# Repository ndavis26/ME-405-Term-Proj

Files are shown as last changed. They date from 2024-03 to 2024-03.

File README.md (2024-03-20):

README.md
=========
Author: Nathaniel Davis
<br>GitHub Repository Link: [ME 405 Term Project](https://github.com/ndavis26/ME-405-Term-Proj)

# Introduction

The purpose of this device is to autonomously aim a NERF blaster at a target and fire it after the program is started. The device was designed to follow a NERF turret [dueling procedure](#dueling-procedure) between two opposing teams.

It is intended for use by children, with a similar use case as other foam-flinging toys, where the goal is to pelt friends and "foes" alike with harmless foam darts. However, the use of the design can reach far beyond foam darts. Given that the sensor detects heat signatures and operates based off of the greatest heat signature, the code can be used for other applications, such as autonomous fire control, where the device would aim water at a fire's greatest heat location to douse the fire (most often its base, which is where a fire should be targeted with water).

<br/><br/>

# Hardware

## Physical Contruction

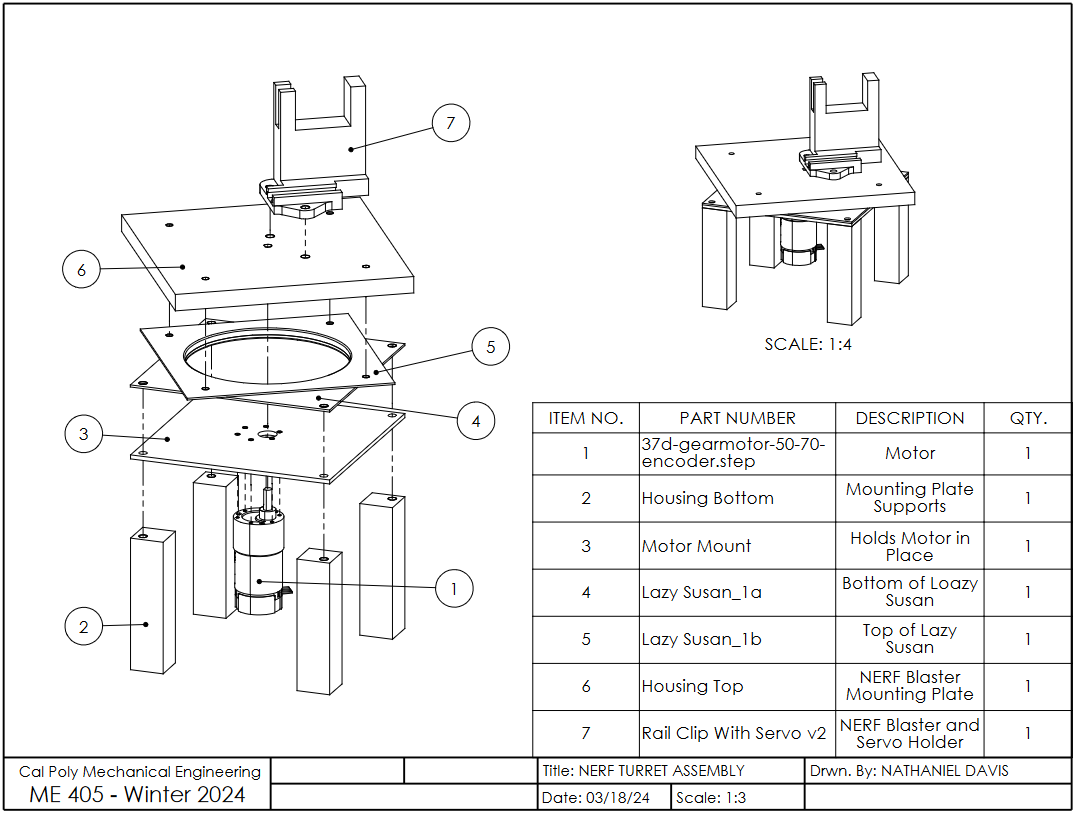
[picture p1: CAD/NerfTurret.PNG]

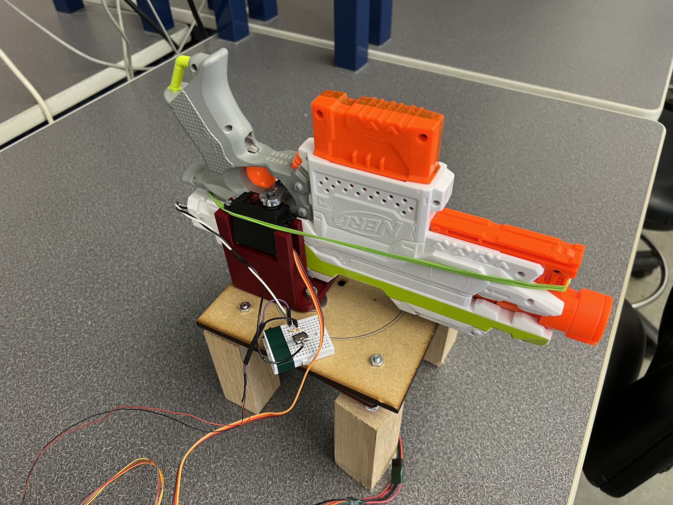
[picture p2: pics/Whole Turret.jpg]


The hardware involved features a modified NERF blaster toy to fire the darts.[^1] This blaster is staged upon a flat plate that is on top of a lazy susan bearing. On the underside of the lazy susan bearing, there is a motor mounting plate. When the motor is mounted to this plate, it connects directly to the blaster base. Although the CAD model shows a single, uniform plate for mounting the NARF blaster, the mounting plate on the current turret uses two plates stacked - one made of acrylic and another made of wood. The acrylic plate is to ensure that there is no deformation, since the motor directly drives the plate on its shaft and acrylic is extremely brittle. The wood plate ensures that there is enough thickness that the motor shaft does not stick out. A list of materials sourced from outside of the mechatronics lab is included in the [Materials](#materials) appendix.

[^1]: Given that NERF brand toys are not *guns* (which fire *bullets*), they will be referred to as *"blasters"* throughout this document (which fire *darts*).

## Circuitry

The circuitry for this device is relatively simple. There are 4 main peripheral electronics to the Nucleo. They are the main motor with encoder, the servo motor, the IR camera, and the NERF flywheels. Although all three are controlled by the Nucleo, the main motor and servo motor are powered by the 12V bench power supply and the flywheels are powered by the 6V battery pack inside of the NERF blaster. The pin connections and any relevant circuit diagrams are included below.

### Main Motor

| **Motor and Encoder Pin** | **Nucleo Pin** |
|---|---|
| Motor Power A | PB4 |
| Motor Power B | PB5 |
| Encoder V_cc | Power Supply 12V |
| Encoder Ground | GND |
| Encoder A Output | PC6 |
| Encoder B Output | PC7 |

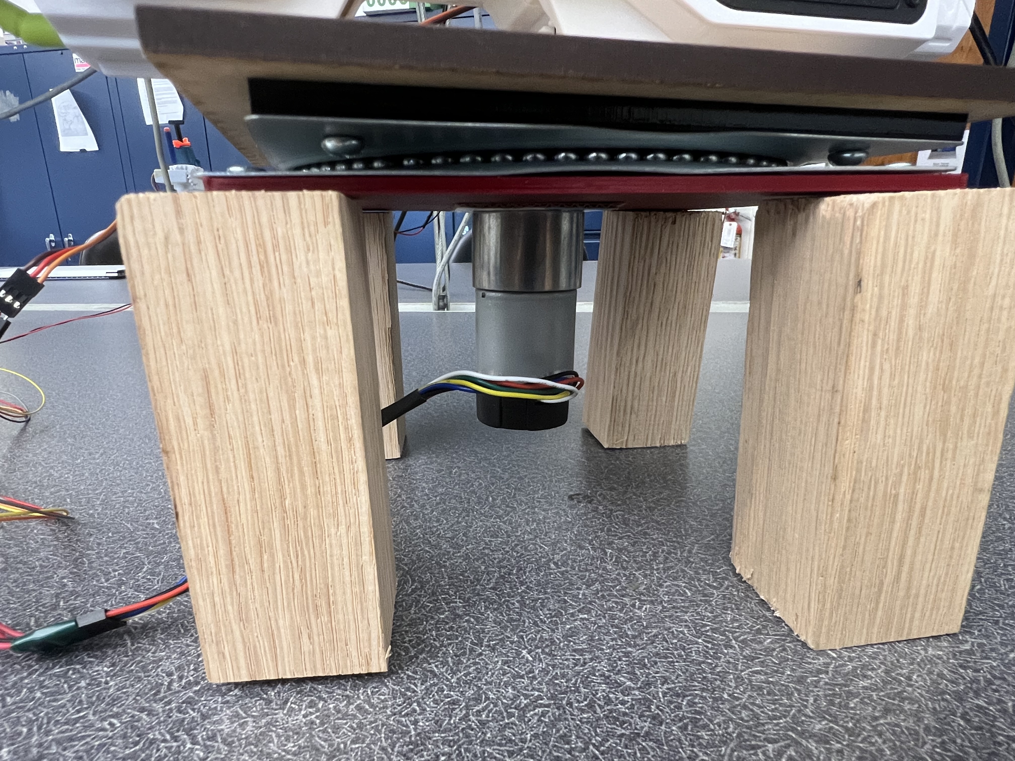
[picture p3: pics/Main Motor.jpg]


This motor has 64 ticks per revolution internally. Given that the output ratio is 50:1, the motor effectively has 3200 ticks per revolution, which is the autoreload value used in the coding.

### Servo Motor

| **Servo Motor Pin** | **Nucleo Pin** |
|---|---|
| Servo Control | PB6 |
| V_in | Power Supply 12V |
| Servo Ground | GND |

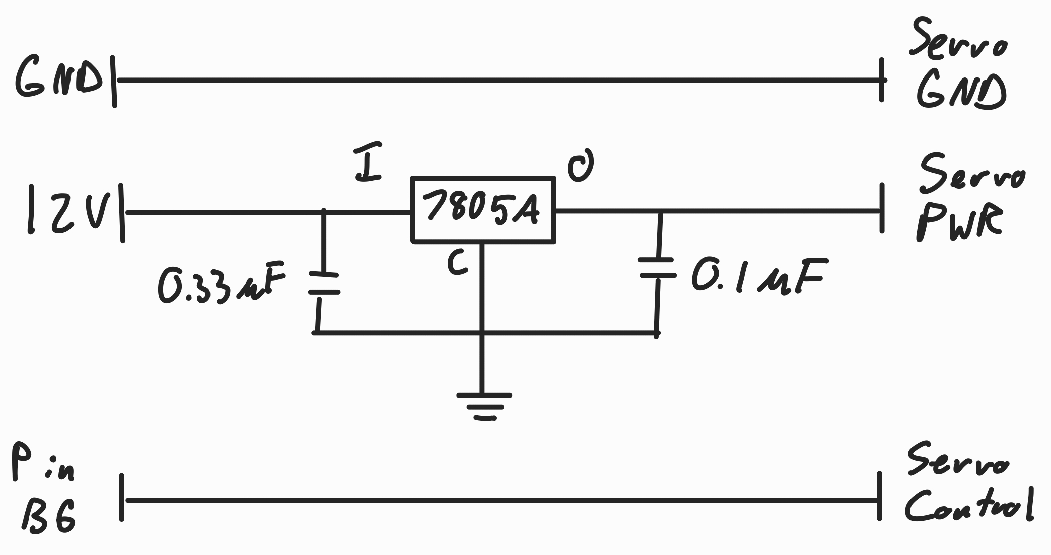
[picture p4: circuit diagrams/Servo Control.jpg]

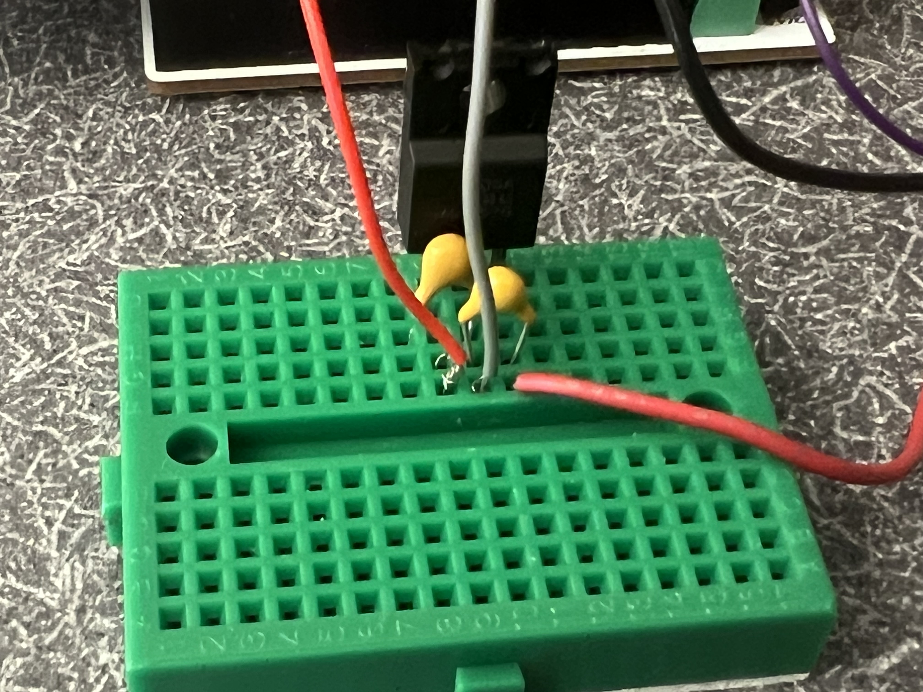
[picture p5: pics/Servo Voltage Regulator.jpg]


Since the servo motor cannot handle 12 volts of power, it must use a voltage regulator to keep the servo power at 5 volts.

### IR Camera

| **IR Camera Pin** | **Nucleo Pin** |
|---|---|
| V_in | 3V3 |
| Ground | GND |
| SDA | PB9 |
| SCL | PB8 |

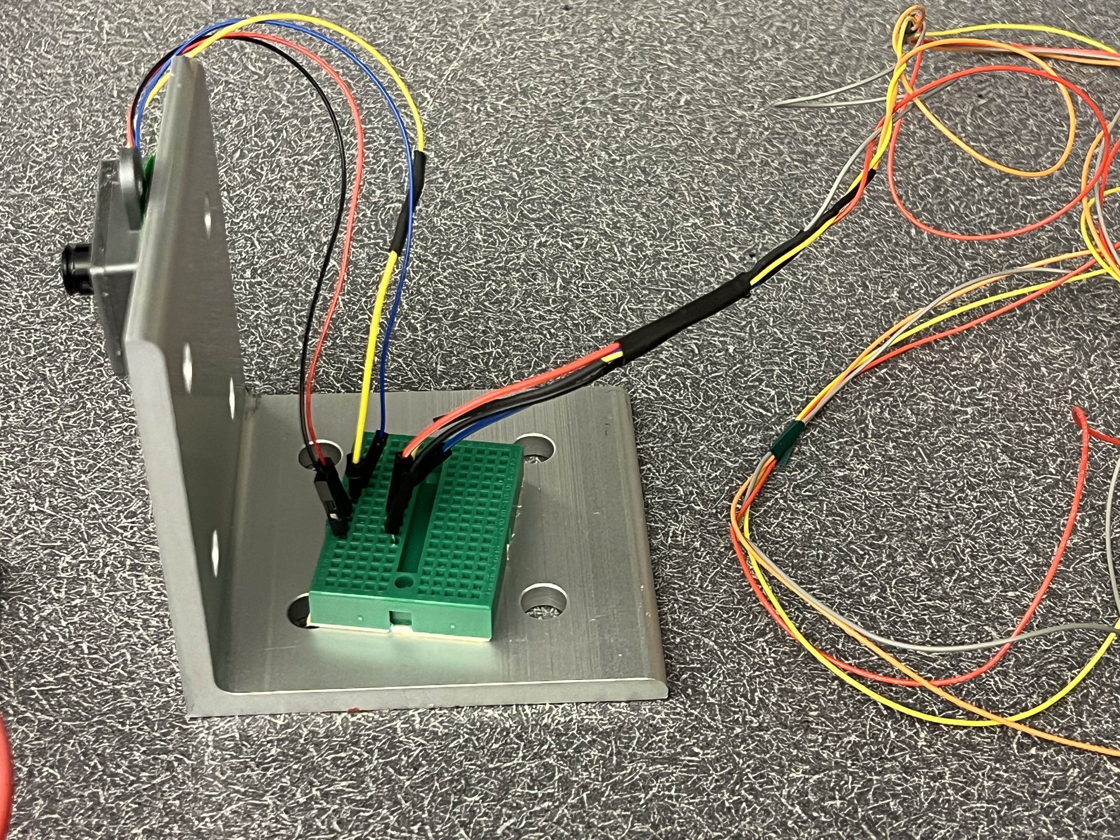
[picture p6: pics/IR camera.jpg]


### Flywheels

| **Flywheel Pin** | **Nucleo Pin** |
|---|---|
| MOSFET Gate | PC3 |
| Ground | GND |

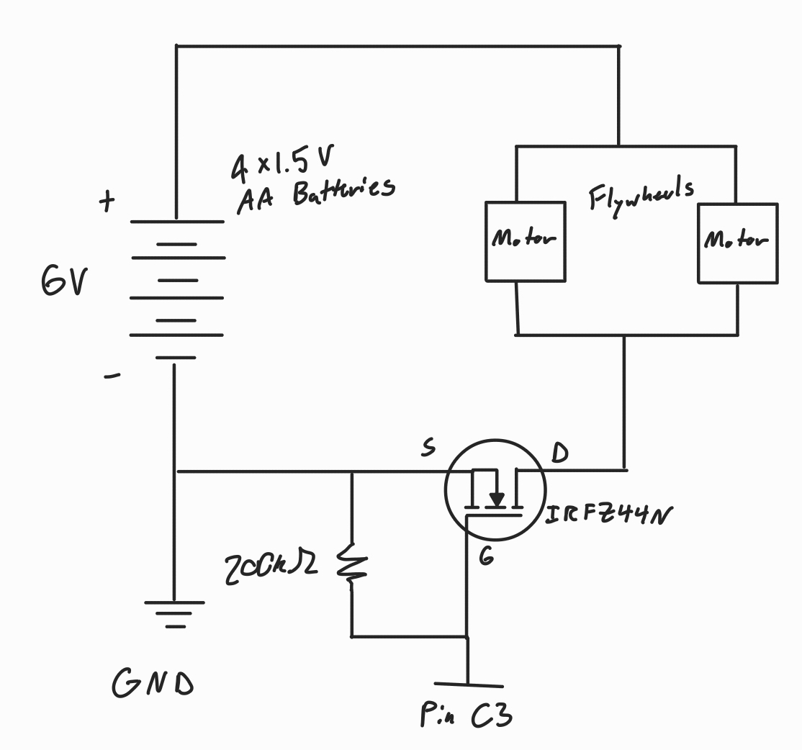
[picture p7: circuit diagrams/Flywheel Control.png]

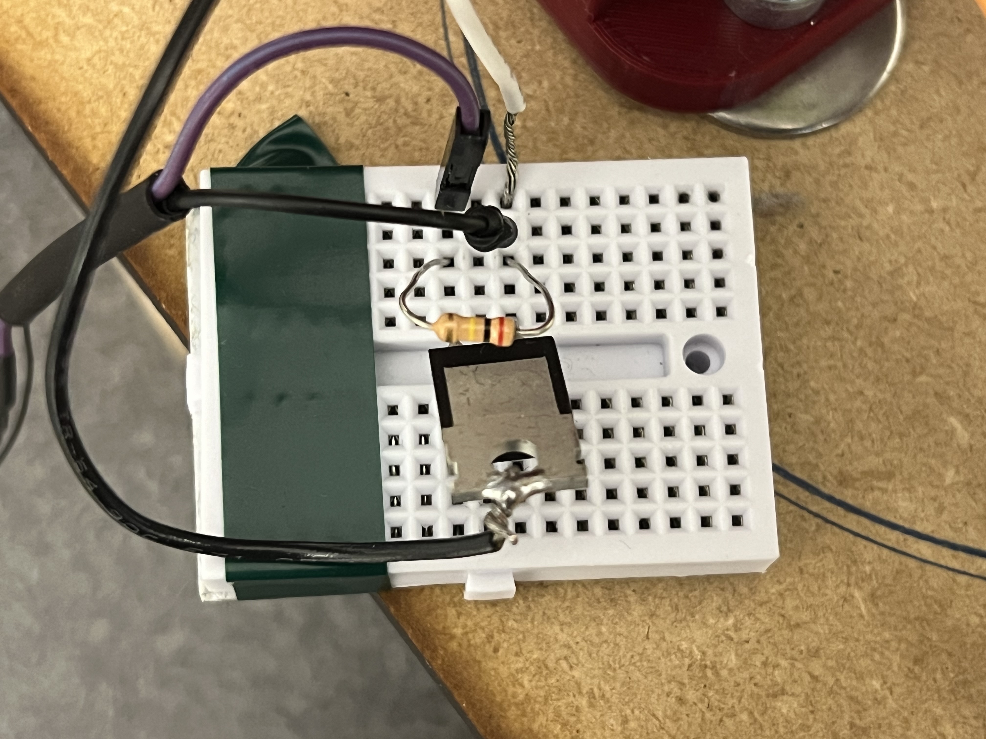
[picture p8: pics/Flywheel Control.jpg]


Pin C3 is used to control the NERF flyhweels.

<br/><br/>

# Software

The dueling is completed in 7 repeating steps, besides intialization. The peripheral(s) used during the step are shown in italics:

1. Wait for button press.
2. Turn to face opponent. *-Motor*
3. Wait 5 seconds.
4. Check current position of opponent. *-IR camera*
5. Adjust aim. *-Motor*
6. Fire. *-Servo, Flywheels*
7. Turn back around and reset to Step 1. *-Motor*

## Files

The files used are:
* [main_v3.py](https://github.com/ndavis26/ME-405-Term-Proj/blob/main/src/main_v3.py) - Holds the tasks and states of the device.
* [motor_driver_updated.py](https://github.com/ndavis26/ME-405-Term-Proj/blob/main/src/motor_driver_updated.py) - Reference for motor class object. This class sets the PWM of the motor.
* [encoder_reader_updated.py](https://github.com/ndavis26/ME-405-Term-Proj/blob/main/src/encoder_reader_updated.py) - Reference for encoder class object. This class reads the motor encoder.
* [motorwithencoder_updated.py](https://github.com/ndavis26/ME-405-Term-Proj/blob/main/src/motorwithencoder_updated.py) -  Reference for the motor controller class object. This class controls the motor through PI control.
* [servo.py](https://github.com/ndavis26/ME-405-Term-Proj/blob/main/src/servo.py) -  Reference for the servo class object. This class controls the servo through pulse width signals.
* [mlx_cam.py](https://github.com/ndavis26/ME-405-Term-Proj/blob/main/src/mlx_cam.py) - Reference for the IR camera class object. This class takes pictures using the IR camera by TWI communication. Original file is sourced from the [ME405-Support GitHub repository](https://github.com/spluttflob/ME405-Support).

The full Doxygen documentation of all the files can be found [here](https://ndavis26.github.io/ME-405-Term-Proj/).

## Tasks / States

Due to the sequential nature of the dueling procedure, only two tasks are needed. 

### Task 1: Mastermind
The first task handles the looping dueling procedure. It involves 7 states. There is only 1 intertask variable, *motor_setpoint*, which stores the motor setpoint. This task has a priority of 1 and a period of 20 ms.

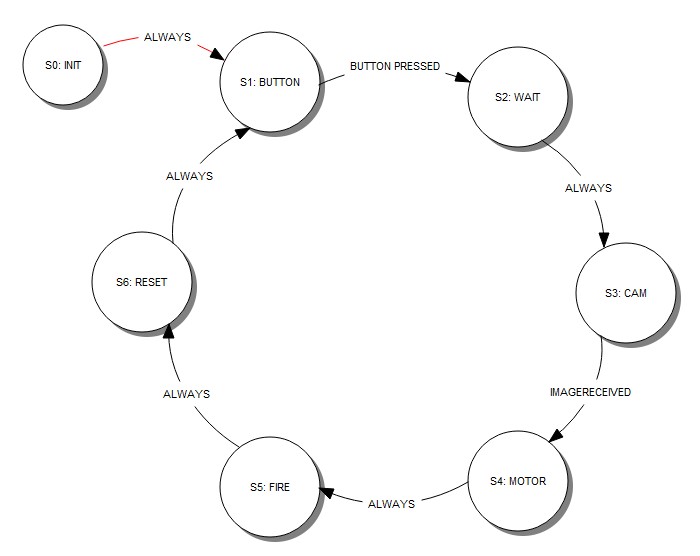
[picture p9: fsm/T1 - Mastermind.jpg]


**S0: INIT** <br>
This state intializes the system. It sets the servo control pins, the flywheel pins, the start button on the Nucleo, and initializes the IR camera.

**S1: BUTTON** <br>
Repeatedly checks if the blue button on the Nucleo has been pressed. If it has been pressed, the state transitions to state 2. If not pressed, the state does nothing and yields.

**S2: WAIT** <br>
Turns around the NERF blaster 180 degrees and waits for 5 seconds. The state accomplishes this by waiting for 10 ms intervals at a time and yielding in between each interval.

**S3: CAM** <br>
This state checks if an image has been captured from the IR camera. If no image has been captured, the state does nothing and yields. If there is an image, the state finds the line within the data with the greatest heat value sum and produces an angle to turn to.

**S4: MOTOR** <br>
Using the angle produced in state 3, the motor setpoint is adjusted to achieve the desired angle.

**S5: FIRE** <br>
This state starts the uninterruptible firing sequence:
1. Flywheels on
2. Servo pulls trigger
3. Flywheels off
4. Servo returns to its original position

**S6: RESET** <br>
Turns the blaster back around and resets to state 1.

### Task 2: Motor Control
The second task simply handles the motor control. It constantly tries to reach the motor setpoint defined by the *motor_setpoint* intertask variable. The motor controller uses PI control to accurately (albeit slowly) obtain the proper angle. There are only 2 states. This task has a priority of 1 and a period of 10 ms.

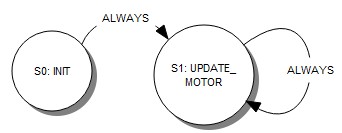
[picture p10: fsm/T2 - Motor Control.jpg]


**S0: INIT** <br>
This state intializes the motor control. Here, the motor and encoder pins are defined and the motor, encoder, and motor controller class objects are created.

**S1: UPDATE_MOTOR** <br>
Repeatedly udpates the PWM to the motor through PI control. The setpoint used is pulled from motor_setpoint.

<br/><br/>

# Results

## Testing

The overall system was tested through repeated dueling, but individual components were tested through different means. 

The motor control was tested by repeatedly having the system rotate 180 degrees as well as having it do small aiming adjustments. The Kp and Ki were then adjusted until both procedures could be performed in an acceptable amount of time. 

The camera was tested by standing at different angles relative to the IR camera and adjusting the angle it gives based on the IR picture it takes.

The flywheel and servo control were tested using the [firing test.py](https://github.com/ndavis26/ME-405-Term-Proj/blob/main/src/test/firing%20test.py) file. This test was used to tune the duration of the servo movement.

## Improvements and Recomendations

Unfortunately there are many flaws to this system.

The device can properly turn to face the opponent, check the camera, adjust accordingly, and turn on the flywheels, but is unfortunately unable to fire darts in its current state due to the servo's malfunction.

The first flaw is the trigger system. The first servo we used drew too much current, which I did not discover until later in the project. While testing the servo and firing procedure, I had been using my desktop computer as the USB power source for the Nucleo, which had sufficient current supply. However, when I began to use my laptop, the current draw (which exceeded the ~0.5 amp fuse in the USB port), it shut my laptop off. We began to search for other solutions, including using a voltage regulator combined with the 12V power supply, which only works some of the time[^2]. If the torque of the motor ever accidentally exceeds a certain amount, the voltage regulator will drop to 1 volt supplied to the servo. If given more time, a more robust servo trigger system would be devloped. It would require a combination of circuit redesign to get the current needed to the servo as well as manufacturing redesign to make sure the servo motor does not have to exert as much effort (and can pull the trigger more reliably).

[^2]: The 12V power supply also had to be set to 1.5 A to make it less likely that the current draw did not exceed the power supply's current source.

The second flaw is in the PI motor control. The first and last moves of the duel are large, 180 degree turns that do not need to be accurate but need to be quick. In this case, a larger Kp and a smaller Ki is desired, as too large of a Ki causes the motor to overshoot by a large amount and then swing across the desired setpoint wildly. During the fine targeting after receiving the camera info, however, there is only a small difference between the motor's current position and the desired setpoint. In this case, a larger Ki is desired to make that small difference matter and provide more rapid fine adjustment. If given more time, more intertask variables would be implemented to allow control of the Ki and Kp values from Task 1: Mastermind to adjust the Kp and Ki during each move.

The third flaw is in the motor shaft power transfer. There is too much tolerance between the motor shaft and the blaster base plate. Although the motor can supply the necessary torque to spin the plate, an independent geared system would have better sufficed to allow greater precision in the angle. This is compounded by the fact that the motor chosen only has 3200 ticks per revolution (as compared to the standard ME 405 kit's motor with 65535 ticks per revolution).

The final flaw is in the IR adjustment. It is not well tuned. This is also due to the motor control inacurracy decribed in the third flaw.

<br/><br/>

# Appendix

## Materials

| **Item** | **Source** | **Link to Purchase or Info** | **Function** | **Quantity** |
|---|---|---|---|---|
| NERF Modulus Stryfe Blaster | Amazon | [Purchase](https://www.amazon.com/NERF-Motorized-Extension-Official-Exclusive/dp/B06XWF6NYW) | Fires foam dart | 1 |
| Polulu 50:1 Metal Gearmotor  | Robotics Club | [Info](https://www.pololu.com/product/4753/specs) | Drives blaster base plate | 1 |
| Lazy Susan  | Amazon | [Purchase](https://www.amazon.com/Turntable-bearing-rotating-cabinet-profile/dp/B08N52SVXF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) | Allows rotation between <br>motor mount and blaster base plate | 1 |
| Mounting Plate - Wood | Manufactured - Laser Cut | N/A | Blaster mounting top plate | 1 |
| Mounting Plate - Acrylic | Manufactured - Laser Cut | N/A | Blaster mounting bottom plate | 1 |
| Motor Mounting Plate | 3D Printed | N/A | Motor mounting plate | 1 |
| Rail Clip with Servo  | 3D Printed | N/A | Connects servo, blaster, and <br>base plate | 1 |
| Towerpro MG995 | Robotics Club | [Info](https://servodatabase.com/servo/towerpro/mg995) | Pulls blaster trigger | 1 |
| IRFZ44N | Amazon | [Purchase](https://www.amazon.com/dp/B07MW1N4Q5?psc=1&ref=ppx_yo2ov_dt_b_product_details) | MOSFET for controlling blaster<br>flywheels | 1 |
| M3-0.5 Screws, 8 mm, 4-pack | Home Depot | N/A | Motor mounting screws | 2 |
| #10-32 Machine Screws and Nuts Combo,<br>3/4", 8-pack | Home Depot | N/A | Holds together base plate | 2 |
| #12 Wood Screws, 1-1/2", 3-pack | Home Depot | N/A | Attaches lower half of lazy susan<br>and motor mounting plate to wooden<br>supports | 2 |
| Wooden Legs, 4" | Home Depot | N/A | Turret supports | 4 |
| Metal L-Bracket | Robotics Club | N/A | IR camera mount | 1 |

## Dueling Procedure 
*Referenced from the Term Project Instructions*

To conduct a duel, each team will first place its launcher on a table, with the launchers several paces apart (the distance may be adjusted) and pointing 180° away from the opposing team’s launcher. A member of each team will stand directly behind the table on which the launcher sits, with safety glasses on and entirely behind the table (not off to the sides), against the edge of the table. No decoys or IR blocking methods may be used.

At a start signal from the Second (the dropping of a handkerchief, of course), each launcher’s power will be turned on. Each team member will have five seconds to move horizontally while standing behind the table, keeping at all times behind and not to the sides of the table, standing and facing directly toward their opponent. After those five seconds, the Second will call “Freeze.” For the following ten seconds, each opponent must remain in a fixed position. Each team’s launcher may launch a projectile at their opponent at any time during the ten seconds just described. Any projectile launched after the ten seconds will be considered a miss regardless of where it goes.

After ten seconds frozen or after being struck, an opponent may move as desired.

A projectile which strikes the opponent as the first solid object hit after its flight from the launcher is scored as a hit; any other outcome (including striking the target after bouncing from another object) is a miss.

If an opponent stands behind the launcher, a hit to the launcher will be counted as a hit to the opponent.

Points will be scored for hits and misses as follows:

| **Result** | **Points** |
|---|---|
| First hit by first team to hit opponent's target | 3 |
| First hit by second team to hit opponent's target | 1 |
| Subsequent hits (overkill...) | 0 |
| Misses (collateral damage is ungentlepersonly) | -1 |

The winner of a duel is the team which scores more highly than its opponents during a given duel. Duels will be done in (best-of-x, x = 2n + 1, n ∈ Z*) sets.

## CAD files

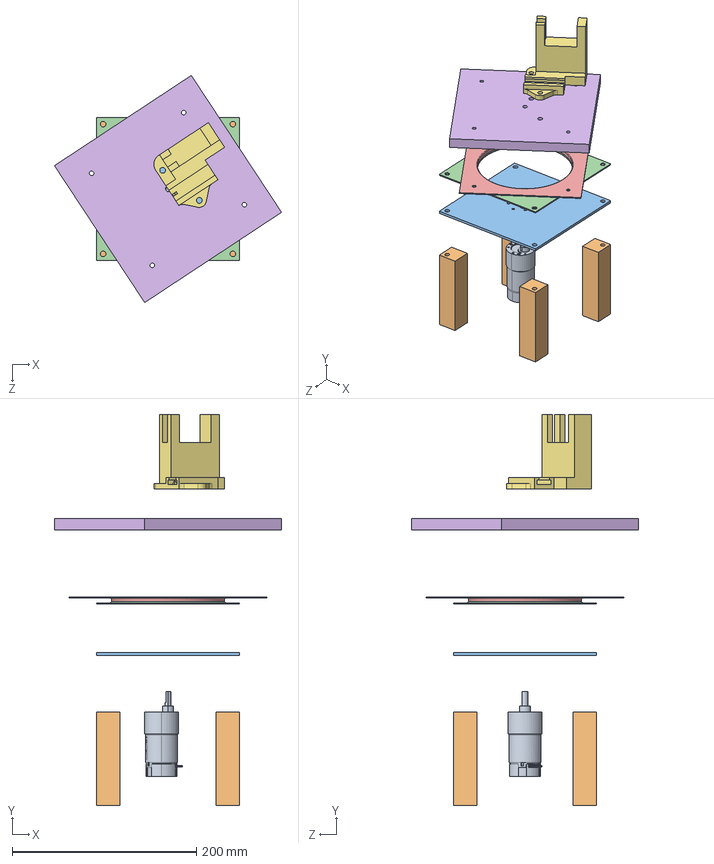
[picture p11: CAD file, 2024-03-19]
CAD/NerfTurret.SLDASM
246.3 x 424.0 x 246.3 mm
37d-gearmotor-50-70-encoder.step
Housing Bottom
Motor Mount
Lazy Susan_1a
Lazy Susan_1b
Housing Top
Rail Clip With Servo v2

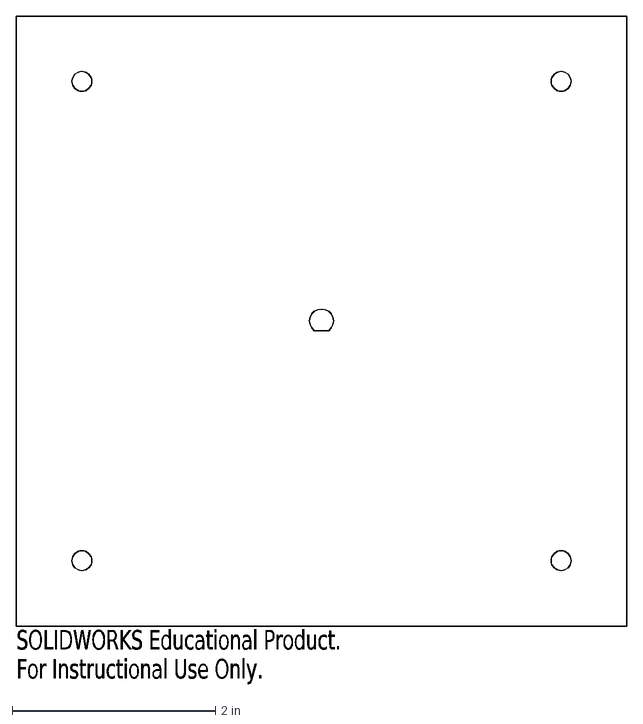
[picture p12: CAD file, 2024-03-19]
CAD/Dxfs/Housing Top Modified.DXF
SOLIDWORKS Educational Product.
For Instructional Use Only.

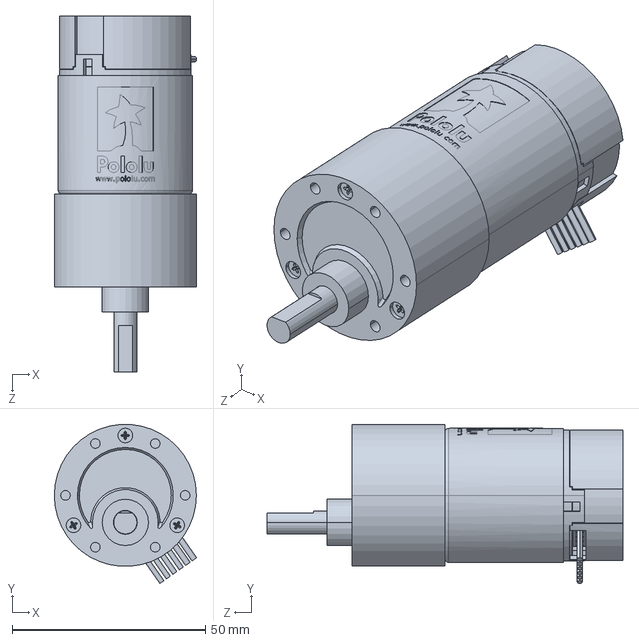
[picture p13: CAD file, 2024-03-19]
CAD/37d-gearmotor-50-70-encoder.step.SLDPRT
36.9 x 41.2 x 92.1 mm

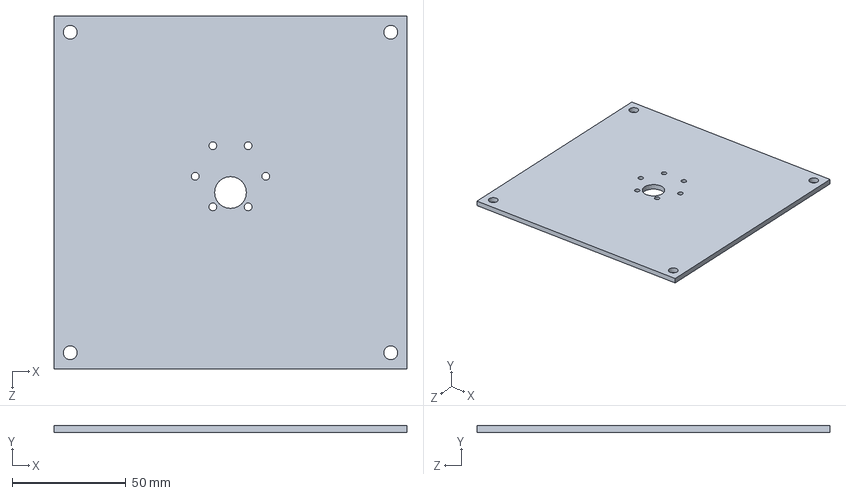
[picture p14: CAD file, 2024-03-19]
CAD/Motor Mount.SLDPRT
154.9 x 3.17 x 154.9 mm

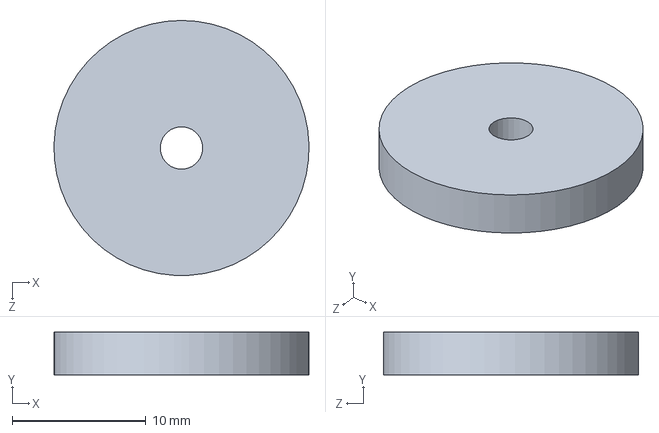
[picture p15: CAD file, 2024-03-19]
CAD/servo ext.SLDPRT
19.0 x 3.17 x 19.1 mm

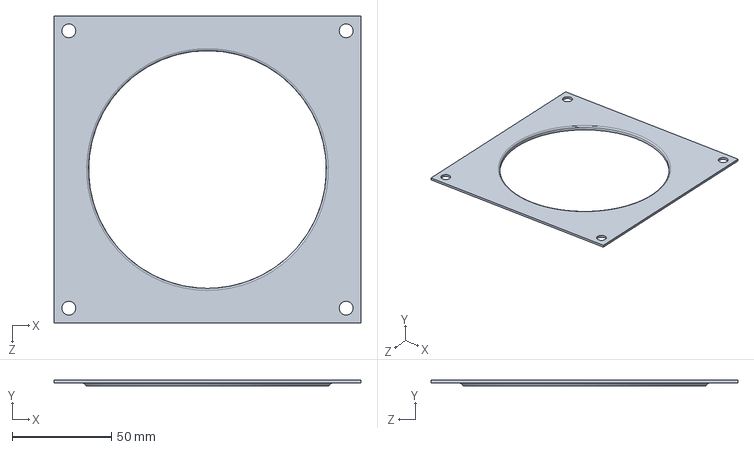
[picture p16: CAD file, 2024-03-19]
CAD/Lazy Susan_1a.SLDPRT
155.0 x 3.00 x 155.0 mm

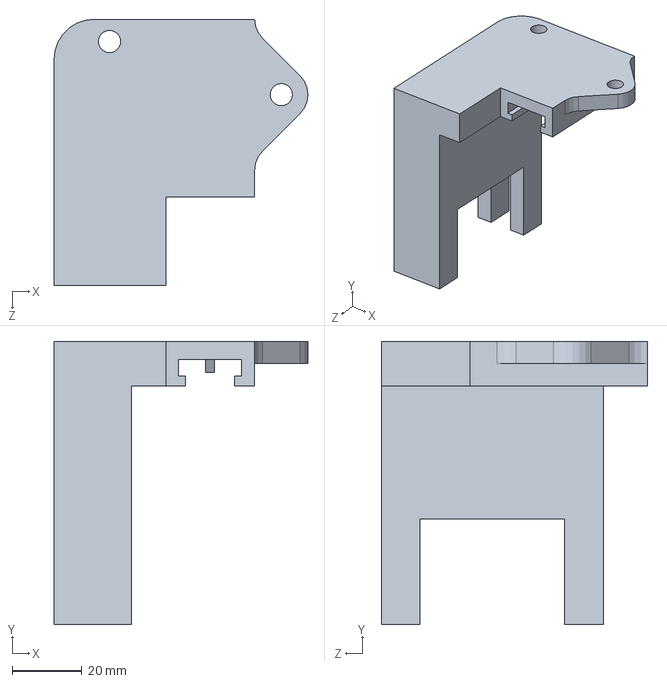
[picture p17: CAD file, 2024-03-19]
CAD/Rail Clip With Servo v2.SLDPRT
72.6 x 81.0 x 76.2 mm

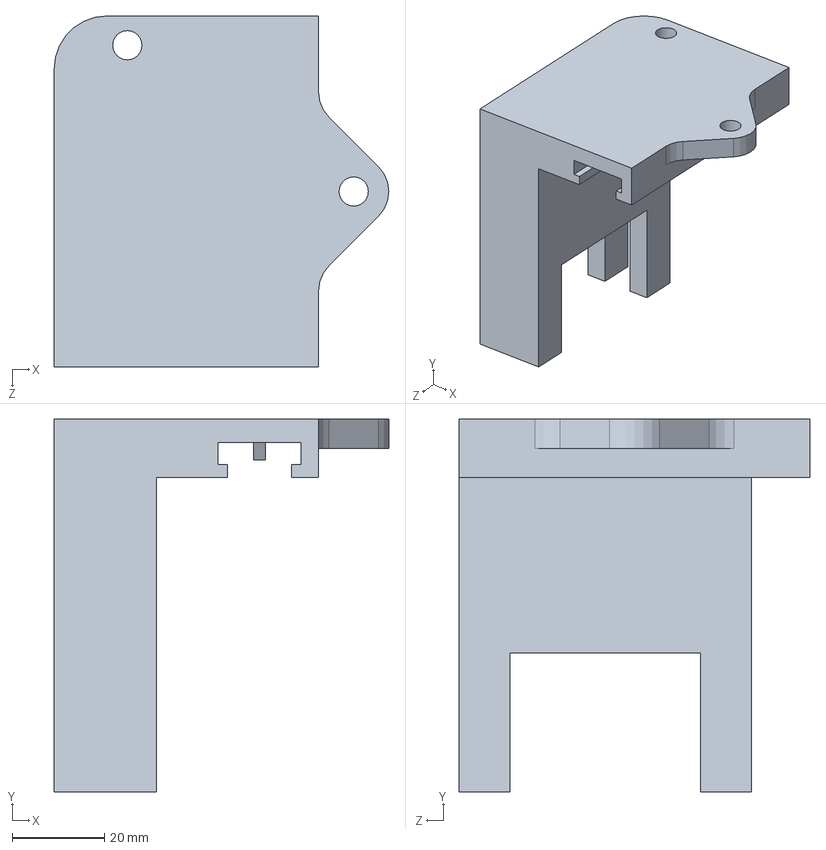
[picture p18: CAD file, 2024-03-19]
CAD/Rail Clip With Servo.SLDPRT
72.6 x 81.0 x 76.2 mm

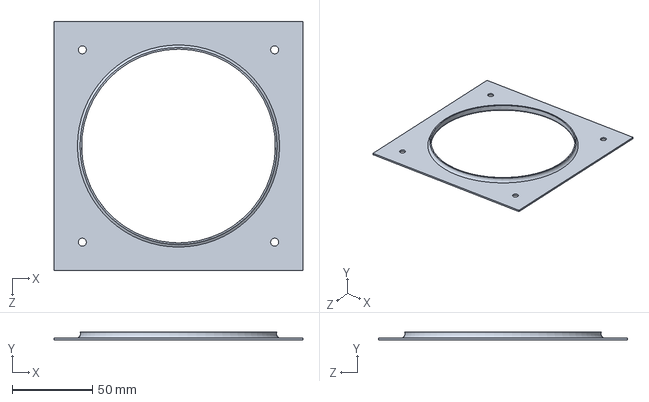
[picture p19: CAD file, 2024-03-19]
CAD/Lazy Susan_1b.SLDPRT
155.0 x 5.00 x 155.0 mm

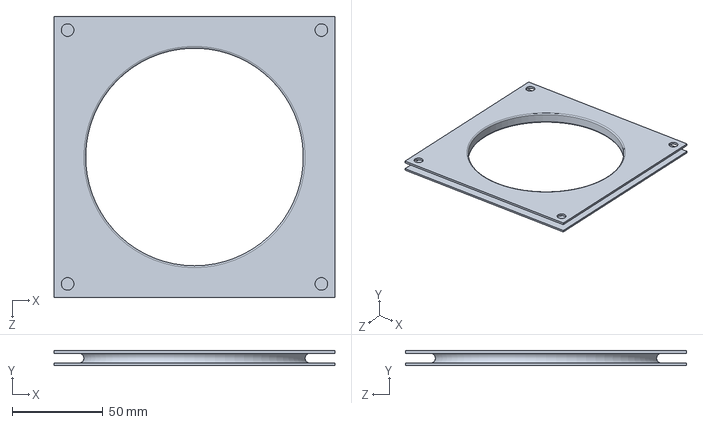
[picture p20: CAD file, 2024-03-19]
CAD/Lazy Susan.SLDPRT
155.0 x 8.00 x 155.0 mm

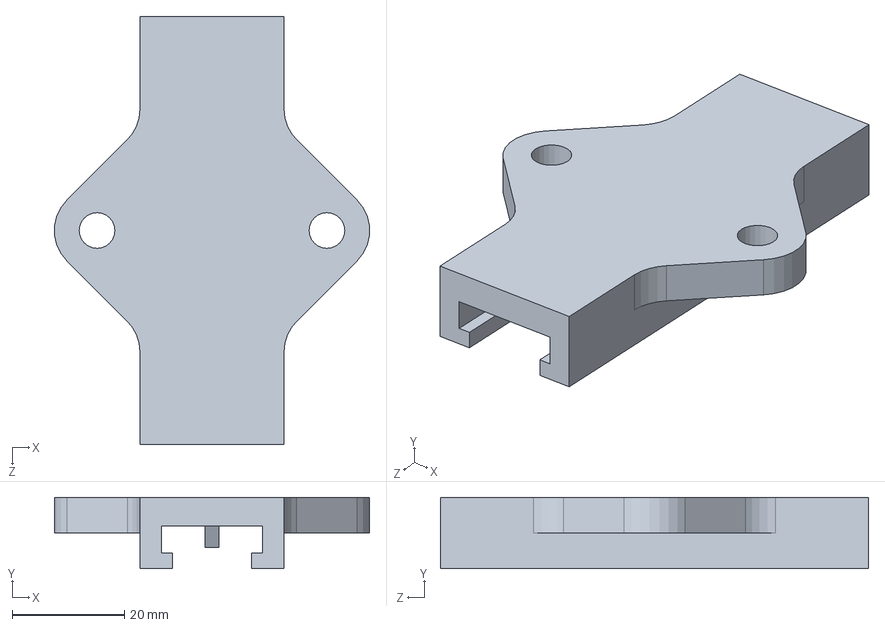
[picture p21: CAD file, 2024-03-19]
CAD/Rail Clip.SLDPRT
56.0 x 12.7 x 76.2 mm

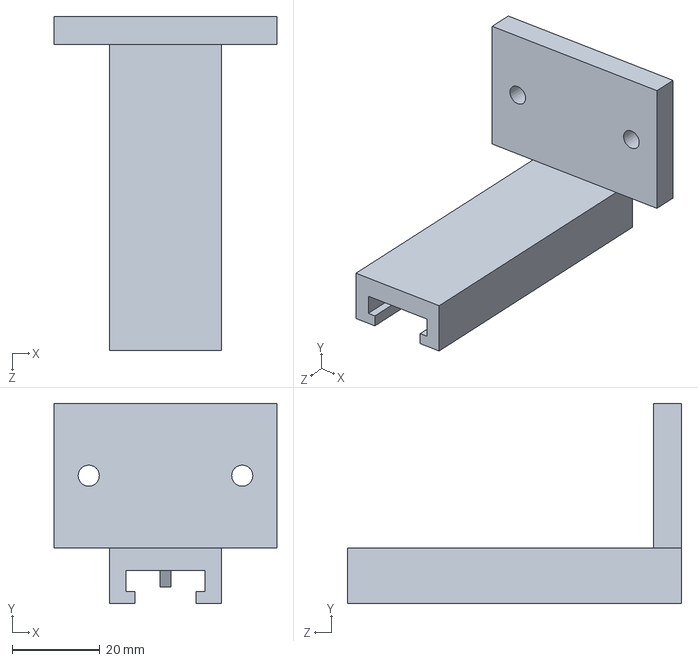
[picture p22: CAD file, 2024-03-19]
CAD/Rail Clip For IR Cam.SLDPRT
50.8 x 45.7 x 76.2 mm

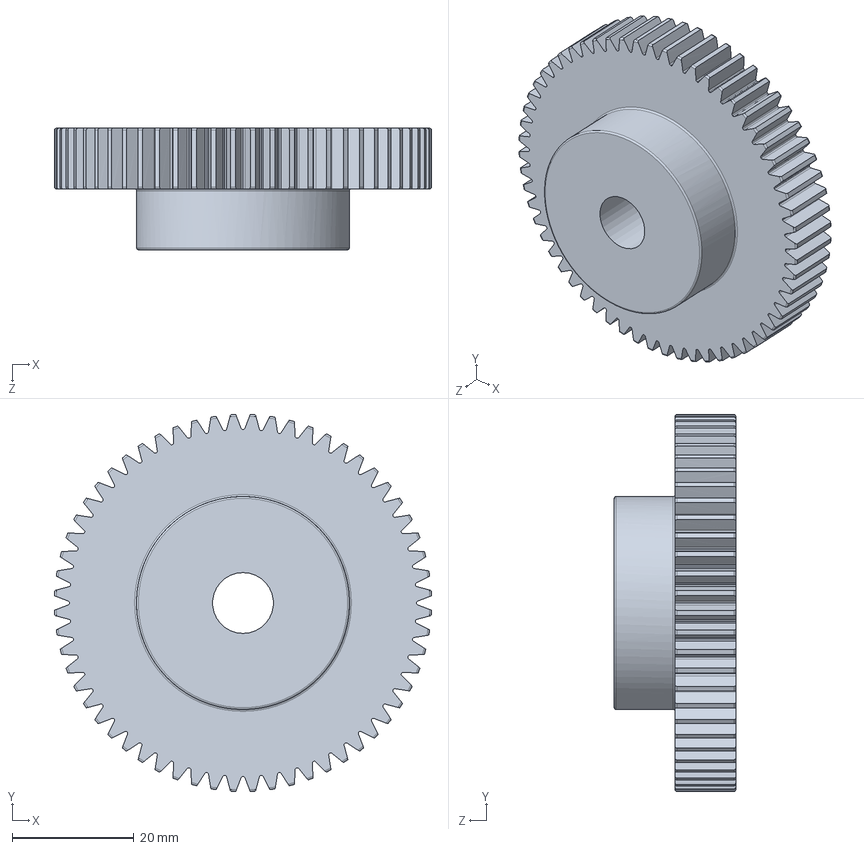
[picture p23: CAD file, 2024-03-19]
CAD/2662N435_20 Degree Pressure Angle Plastic Gear.SLDPRT
62.0 x 62.0 x 20.0 mm

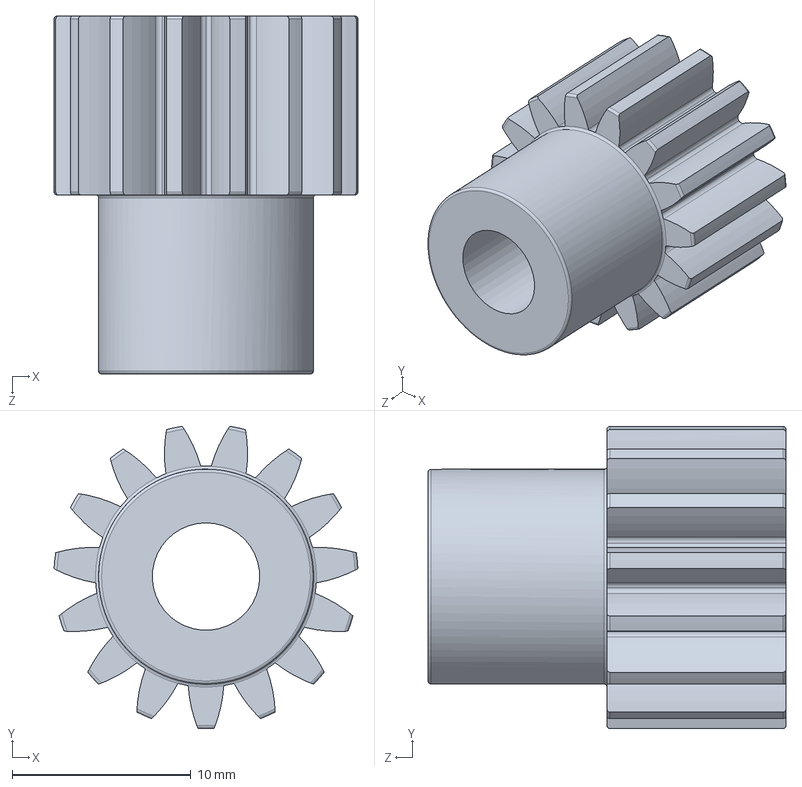
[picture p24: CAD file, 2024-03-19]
CAD/2662N415_20 Degree Pressure Angle Plastic Gear.SLDPRT
17.0 x 16.9 x 20.0 mm

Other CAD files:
CAD/Housing Top.SLDPRT
CAD/Housing Bottom.SLDPRT
CAD/37d-gearmotor-50-70-encoder.step
CAD/Dxfs/Housing Top.DXF
CAD/Dxfs/Motor Mount.DXF
CAD/NerfTurret.SLDDRW
CAD/STLs/Motor Mount.STL
CAD/STLs/Rail Clip For IR Cam.STL
CAD/STLs/Rail Clip With Servo v2.STL
CAD/STLs/Rail Clip With Servo.STL
CAD/STLs/Rail Clip.STL
CAD/STLs/servo ext.STL

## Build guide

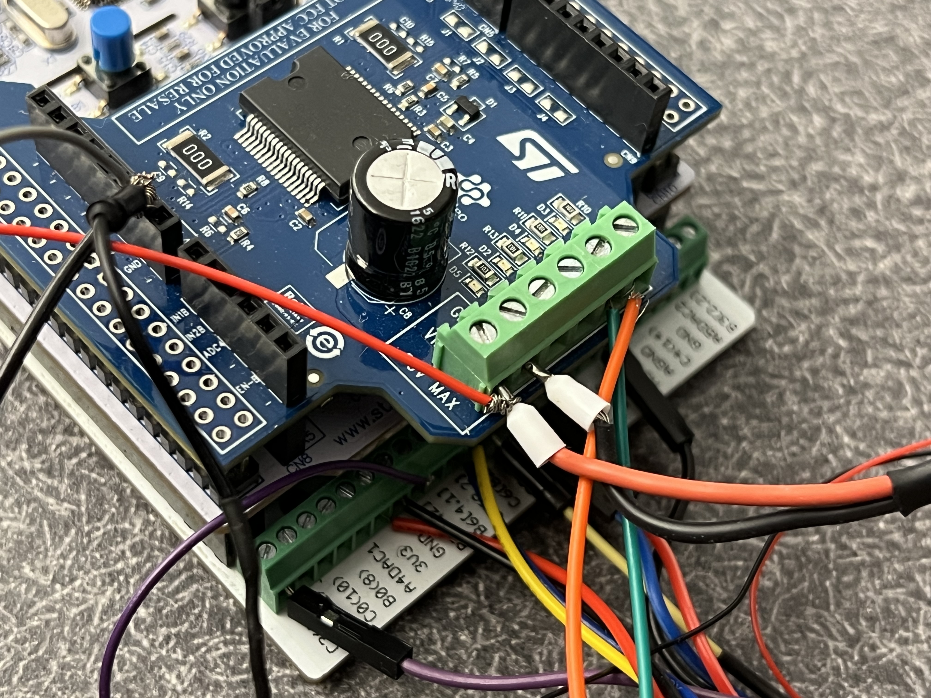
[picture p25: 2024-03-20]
pics/Nucleo Wiring.jpg

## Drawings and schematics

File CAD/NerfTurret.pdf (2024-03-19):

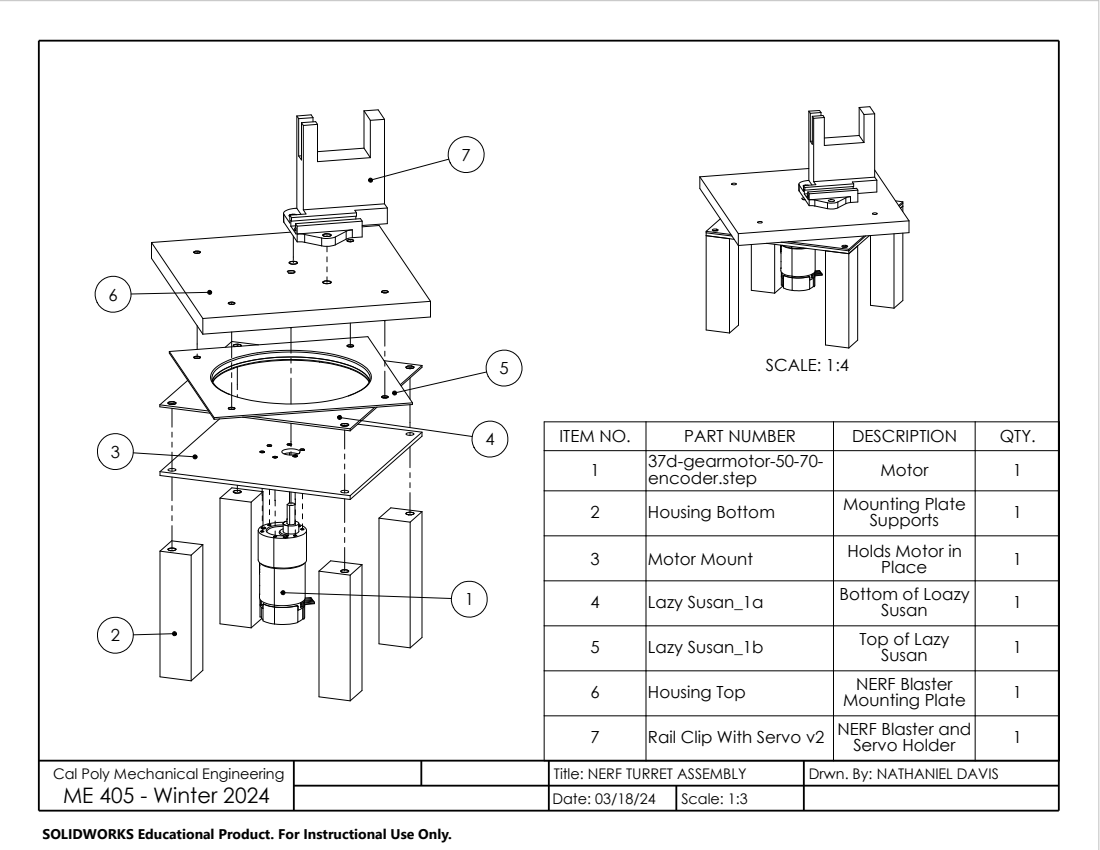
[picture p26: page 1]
SCALE: 1:4

ITEM NO. | PART NUMBER | DESCRIPTION | QTY.
1 | 37d-gearmotor-50-70-encoder.step | Motor | 1

2 | Housing Bottom | Mounting Plate Supports | 1

3 | Motor Mount | Holds Motor in Place | 1

4 | Lazy Susan_1a | Bottom of Loazy Susan | 1

5 | Lazy Susan_1b | Top of Lazy Susan | 1

6 | Housing Top | NERF Blaster Mounting Plate | 1

7 | Rail Clip With Servo v2 | NERF Blaster and Servo Holder | 1

Cal Poly Mechanical Engineering ME 405 - Winter 2024 | | | Title: NERF TURRET ASSEMBLY | Drwn. By: NATHANIEL DAVIS
Date: 03/18/24 | Scale: 1:3

SOLIDWORKS Educational Product. For Instructional Use Only.

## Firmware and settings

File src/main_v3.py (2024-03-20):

"""! @file main_v3.py
ME 405 NERF Turret Term Project
The dueling process is started by pressing the blue button on the Nucleo.
@author Nathaniel Davis
@date 3-19-24
"""

import pyb
import gc
import pyb
import cotask
import task_share
from motor_driver_updated import MotorDriver
from encoder_reader_updated import Encoder 
from motorwithencoder_updated import MotoEncodo
from servo import Servo
from mlx_cam import MLX_Cam
import math
import time
from machine import Pin, I2C
from mlx90640 import MLX90640
from mlx90640.calibration import NUM_ROWS, NUM_COLS, IMAGE_SIZE, TEMP_K
from mlx90640.image import ChessPattern, InterleavedPattern


def task1_mm(shares):
    """!
    controls the main flow of the firing procedure
    @param shares contains the current motor setpoint
    """
    S0_INIT = 0
    S1_BUTTON = 1 
    S2_WAIT = 2
    S3_CAM = 3
    S4_MOTOR = 4
    S5_FIRE = 5
    S6_RESET = 6

    state = S0_INIT
    
    while True:
        motor_setpoint = shares
        if(state == S0_INIT): # initializes system            
            # set up servo
            servpin = pyb.Pin.board.PB6
            servtimer = 4
            servchannel = 1
            serv = Servo(servpin, servtimer, servchannel)

            
            # set up flywheel output
            flypin = pyb.Pin.board.PC3
            flywheel = pyb.Pin(flypin, pyb.Pin.OUT_PP)
            flywheel.low()
            
            #set up button pin
            buttonpin = pyb.Pin.board.PC13
            button = pyb.Pin(buttonpin, pyb.Pin.IN)
            
            
            # Setting up camera - referenced from mlx_cam.py
            # The following import is only used to check if we have an STM32 board such
            # as a Pyboard or Nucleo; if not, use a different library
            try:
                from pyb import info
            # Oops, it's not an STM32; assume generic machine.I2C for ESP32 and others
            except ImportError:
                # For ESP32 38-pin cheapo board from NodeMCU, KeeYees, etc.
                i2c_bus = I2C(1, scl=Pin(22), sda=Pin(21))
            # OK, we do have an STM32, so just use the default pin assignments for I2C1
            else:
                i2c_bus = I2C(1)
            # Select MLX90640 camera I2C address, normally 0x33, and check the bus
            i2c_address = 0x33
            scanhex = [f"0x{addr:X}" for addr in i2c_bus.scan()]
            # Create the camera object and set it up in default mode
            camera = MLX_Cam(i2c_bus)
            camera._camera.refresh_rate = 1.0
            
            state = S1_BUTTON
            print("waiting for button press")
            yield
        elif(state == S1_BUTTON): # waits for button press
            if not button.value():
                state = S2_WAIT
            yield
        elif(state == S2_WAIT): # turns 180 degrees and waits 6 seconds
            print("waiting to duel")
            motor_setpoint.put(1600)
            for _ in range(500):
                time.sleep_ms(10)
                yield
            state = S3_CAM
            yield
        elif(state == S3_CAM): # takes the currently stored camera info and creates an angle
            print("checking camera")
            image = None
            while not image:
                image = camera.get_image_nonblocking()
                yield
#             camera.ascii_art(image)
            csv = []
            for line in camera.get_csv(image, limits=(0, 99)):
                csv.append(sum([eval(i) for i in line.split(',')]))
            cam_row = csv.index(max(csv))
            angle = cam_row - 12.5
            print(angle)
            print("adjusting")
            state = S4_MOTOR
            yield
            
        elif(state == S4_MOTOR): # moves motor
            motor_setpoint.put(int(1600 + angle*05))
            for _ in range(500):
                time.sleep_ms(10)
                yield
            state = S5_FIRE
            yield
            
        elif(state == S5_FIRE): # fire away!
            print("firing!")
            flywheel.high()
            print("flywheel on")
            firing = 250
            time.sleep(1.5)
            serv.ccw()
            print("trigger")
            time.sleep_ms(firing)
            serv.stop()
            time.sleep(0.5)
            serv.cw()
            time.sleep_ms(firing)
            serv.stop()
            time.sleep(0.5)
            serv.off()
            flywheel.low()
            print("flywheel off")
            state = S6_RESET
            yield
        elif(state == S6_RESET): # resets system
            print("reset system")
            motor_setpoint.put(0)
            state = S1_BUTTON
            yield
        
def task2_motorcontrol(shares):
    """!
    motor controller that constantly attmepts to
    reach the setpoint set in the intertask variable "motor_setpoint."
    @param shares contains the current motor setpoint
    """
    S0_INIT = 0
    S1_UPDATE_MOTOR = 1
     
    state = S0_INIT
    while True:
        motor_setpoint = shares
        if(state == S0_INIT): # initializes motor control
            # motor pins
            mtrAplus = pyb.Pin.board.PB4
            Aplusch = 1
            mtrAminus = pyb.Pin.board.PB5
            Aminusch = 2
            mtrEN = pyb.Pin.board.PA10
            mtrtimer = 3

            # encoder pins
            encA = pyb.Pin.board.PC6
            encAch = 1
            encB = pyb.Pin.board.PC7
            encBch = 2
            readch = 8
            
            # set up motor driver
            moe = MotorDriver(mtrEN, mtrAplus, Aplusch,  mtrAminus, Aminusch, mtrtimer)
            # set up encoder
            enc = Encoder(encA, encB, readch, encAch, encBch)
            # set up motor control
            motorctrl = MotoEncodo(moe, enc)
            motorctrl.set_Kp(0.05)
            motorctrl.set_Ki(0.02)
            motor_setpoint.put(0)
            
            state = S1_UPDATE_MOTOR
            yield
            
        elif(state == S1_UPDATE_MOTOR): #constantly updates the motor if there is a motor setpoint
            if motor_setpoint.any():
                setpoint = motor_setpoint.get()
                motorctrl.set_setpoint(setpoint)
                motor_setpoint.put(setpoint)
#                 print(f'setpoint: {setpoint}, current location: {enc.read()}')
            yield
        
if __name__ == "__main__": # run cotask scheduler
    
    # create intertask data here
    motor_setpoint = task_share.Queue('l', 1, thread_protect=True, overwrite=True, name="Motor Setpoint")
    
    # create tasks
    task1 = cotask.Task(task1_mm, name="Mastermind", priority=1, period=20, profile=True, trace=False, shares=(motor_setpoint))
    task2 = cotask.Task(task2_motorcontrol, name="Motor Control", priority=1, period=10, profile=True, trace=False, shares=(motor_setpoint))
    cotask.task_list.append(task1)
    cotask.task_list.append(task2)
    
    # clean up memory
    gc.collect()
    
    # create scheduler
    while True:
        try:
            cotask.task_list.pri_sched()
        except KeyboardInterrupt:
            break
    
    
    

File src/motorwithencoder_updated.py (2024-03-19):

"""! @file closed_loop.py
Defines Servo class.
If this is the main.py file on the Nucleo,
it will run a motor response test.
@author Nathaniel Davis
@author Sebastian Bessoudo
@date 03-19-2024
"""

import micropython
import pyb
import time
import cqueue
from motor_driver_updated import MotorDriver
from encoder_reader_updated import Encoder

# Allow interrupts to display errors
micropython.alloc_emergency_exception_buf(100)

class MotoEncodo:
    """!
    This class uses an already established motor class object and encoder class object so the user can input a Kp value, Ki value,
    and a motor setpoint.
    """
    def __init__(self, motor, encoder):
        """!
        Initializes the servo. Also sets up a 
        @param motor motor class object to be used
        @param encoder encoder class object to be used
        """
        self.motor = motor
        self.encoder = encoder
        self.Kp = 0.1
        self.Ki = 0
        self.error = 0
        self.sum = 0
        
    def run(self, level):
        """!
        sets the duty cycle for the motor to run based on
        @param level duty cycle for the motor between 0-100
        """
        self.motor.set_duty_cycle(level)
        
    def set_setpoint(self, setpoint):
        """!
        sets the setpoint of the motor
        @param setpoint setpoint to have the motor reach
        """
        self.encoder.read()
        self.error = setpoint - self.encoder.pos
        self.sum += self.error
        self.PWM = (self.Kp*self.error)+(self.Ki*self.sum*0.01)
        self.motor.set_duty_cycle(self.PWM)
        
    def set_Kp(self, Kp):
        """!
        sets the Kp value
        @param Kp Kp value desired
        """
        self.Kp = Kp
        
    def set_Ki(self, Ki):
        """!
        sets the Ki value
        @param Ki Ki value desired
        """
        self.Ki = Ki
    def plot_results():
        """!
        Used for running motor and encoder repsonse test.
        """
        position = []
        time = [10*x for x in range(500)]
        for i in range(len(time)):
            positions.append(serv.encoder.read())
            print(time + ', ' + position)
        print('End')

    
if __name__ == "__main__":  
    # run motor response test
    # motor pins
    mtrAplus = pyb.Pin.board.PB4
    Aplusch = 1
    mtrAminus = pyb.Pin.board.PB5
    Aminusch = 2
    mtrEN = pyb.Pin.board.PA10
    mtrtimer = 3

    # encoder pins
    encA = pyb.Pin.board.PC6
    encAch = 1
    encB = pyb.Pin.board.PC7
    encBch = 2
    readch = 8
    
    # set up motor driver
    moe = MotorDriver(mtrEN, mtrAplus, Aplusch,  mtrAminus, Aminusch, mtrtimer)
    # set up encoder
    enc = Encoder(encA, encB, readch, encAch, encBch)
    # set up motor control
    motorctrl = MotoEncodo(moe, enc)
    input_kp = float(input('Please input a value for Kp: '))
    motorctrl.set_Kp(input_kp)
    input_ki = float(input('Please input a value for Ki: '))
    motorctrl.set_Ki(input_ki)
    input_setp = int(input('Please input a value for the setpoint: '))
    while True:
        time.sleep_ms(10)
        motorctrl.set_setpoint(input_setp)
        print(enc.read())
        
            
    

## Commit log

2024-03-19 Added all files to main repository
    Files were accidentally not located in actual repository
    [2662N415_20 Degree Pressure Angle Plastic Gear.SLDPRT, 2662N435_20 Degree Pressure Angle Plastic Gear.SLDPRT, 37d-gearmotor-50-70-encoder.step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]
2024-03-19 README update
    [Housing Bottom.SLDPRT, Housing Top.SLDPRT, NerfTurret.SLDASM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]
